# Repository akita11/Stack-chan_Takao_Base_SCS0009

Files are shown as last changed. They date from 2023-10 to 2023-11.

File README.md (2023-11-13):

# Stack-chan_Takao_Base_SCS0009

現時点で ｽﾀｯｸﾁｬﾝ を組み立てる最もシンプルな方法と思われる、[タカオさん](https://twitter.com/mongonta555)の[タカオ版](https://mongonta.booth.pm/)で[Feetech社のシリアルサーボSCS0009](https://www.switch-science.com/products/8042)を使うためのボードです。（※[SCS0009用のタカオ版筐体](https://github.com/mongonta0716/3DPrinter_Models)とあわせて使用できます。M5Stack本体と2個のシリアルサーボモータSCS0009用コネクタ、給電用のUSB TypeCコネクタがついたボードです。電源スイッチもついています。まるごと一式、タカオ版のサーボ固定部分(Bracket)に収納できます。市販のUSB Type-CコネクタつきのACアダプタ等をつないで給電して使用します。以下のように、本体の後ろ側からUSB Type-Cケーブルで給電して動作させることができます。

## 表面実装部品版

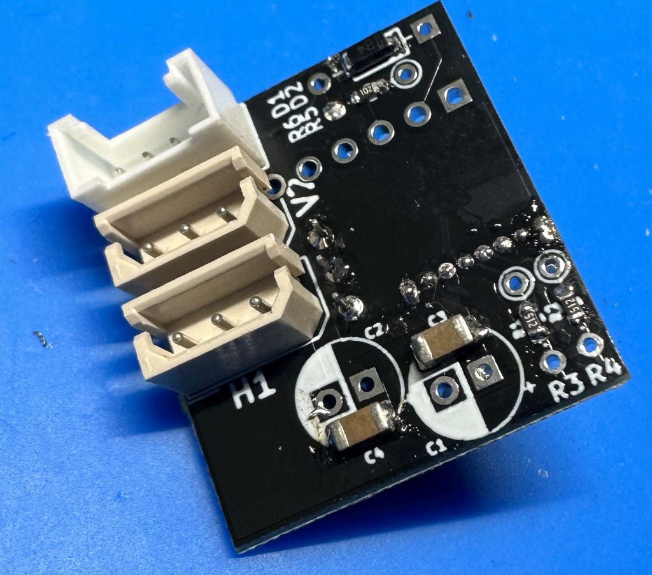
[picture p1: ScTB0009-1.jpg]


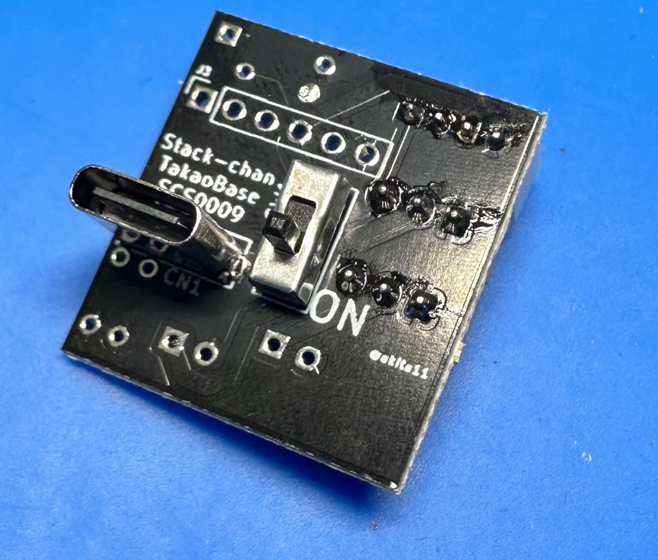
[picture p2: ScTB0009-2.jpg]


※完成品として[スイッチサイエンスで委託販売中](https://www.switch-science.com/products/9288)です

## 挿入実装部品版

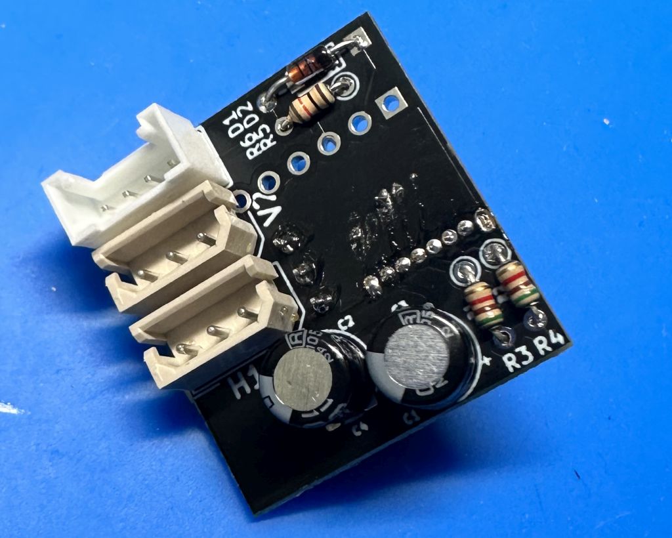
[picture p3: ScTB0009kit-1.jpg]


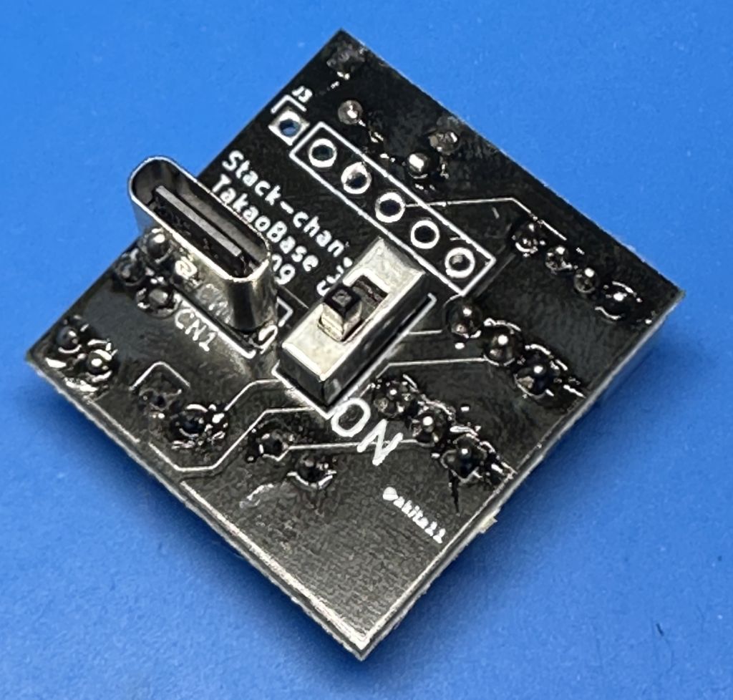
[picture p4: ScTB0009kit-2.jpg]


※部品キットとして[スイッチサイエンスで委託販売中](https://www.switch-science.com/products/9289)です

※部品キット版では、[組み立て手順](https://github.com/akita11/Stack-chan_Takao_Base_SCS0009/blob/main/Build/README.md)に沿って部品をはんだ付けしてください。

## 他に用意するもの

- M5Stack本体 (Core BasicまたはCore2がおすすめ）
- シリアルサーボモータ2個 [Feetech SCS0009](https://www.switch-science.com/products/8042)
- Groveケーブル ([M5Stack用5cm](https://www.switch-science.com/products/8664)など。すでにM5StackのUNITなどで余っているものがあればそれでもOK）
- 筐体[SCS0009用のタカオ版筐体](https://github.com/mongonta0716/3DPrinter_Models)を3Dプリント出力したものと必要なネジ類（[Boothで頒布中](https://booth.pm/ja/items/5186064)）

## 使い方

- 筐体の組み立てなどは、[タカオさんの手順](https://booth.pm/ja/items/5186064)を参考に行います。
- M5Stack本体と本ボードはGroveケーブルで接続します
- 2個のサーボを本ボードに接続します。ボード上の「H1」側には水平方向（足側）のサーボを、「V2」側には上下方向（筐体側）のサーボを接続します。いずれも、サーボのGND側（茶色や黒のケーブル側）を、本ボードの端側（白マークのある側）に挿し込みます。
- 本ボードを、Bracket（サーボを固定している部品）に収めます。必要に応じて両面テープやネジなどで固定してください。

## シリアルサーボSCS0009の設定

Feetech社のシリアルサーボSCS0009は、専用設定ツール[FD](https://gitee.com/ftservo/fddebug)を使ってIDや各種パラメータを設定することができます。特に今回のように2個のSCS0009を別々に使用する場合はそれぞれにIDを設定する必要があります。IDの初期値は1ですので、1つのSCC0009のIDを2に設定する必要があります。SCS0009の設定には[純正のボードFE-URT-1](https://akizukidenshi.com/catalog/g/gM-16295/)を使うこともできますが、このStack-chan_TakaoBaSE_SCS0009は簡易的に設定をするための回路が組み込まれています。ただし簡易的な回路のため、設定の読み出し・書き込みに失敗することもありますので、うまく読み出し・書き込みができない場合は、何度かリトライしてください。
※この回路は、[@washishi](https://twitter.com/washishi)さんの[Xでの投稿](https://twitter.com/washishi/status/1589990730822725632)を参考にしました。

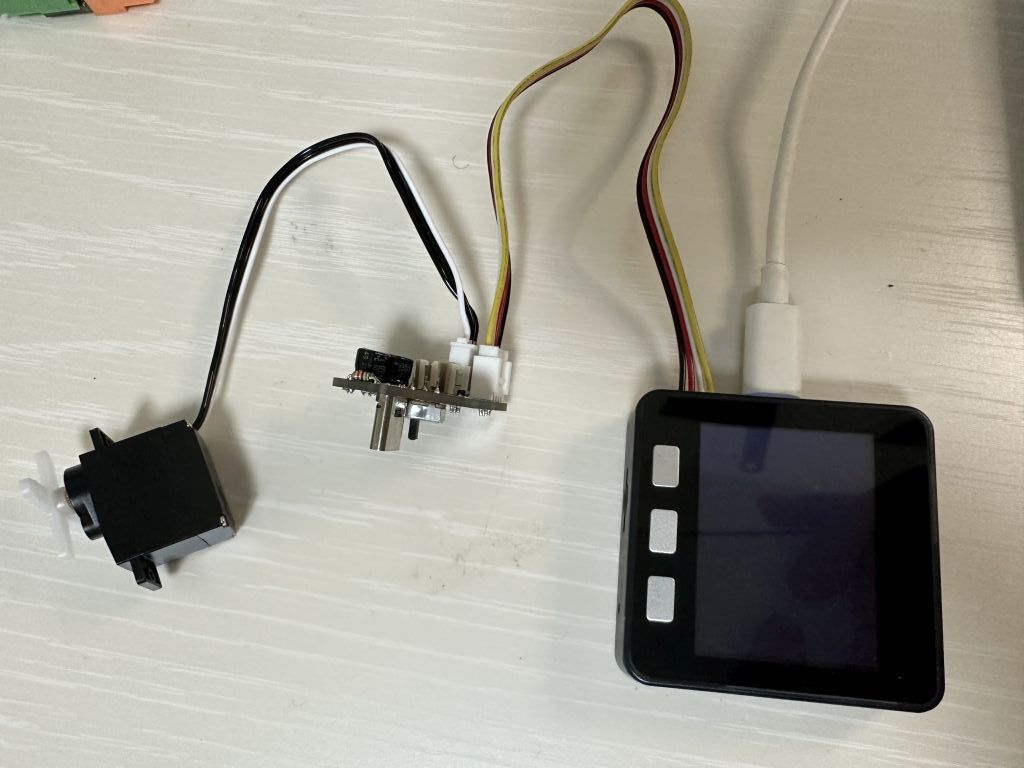
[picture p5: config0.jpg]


M5Stack(Basic/Core2)、本ボード、IDを変更するSCS0009（どちらのコネクタでもOK）を接続する。M5Stackには、設定用プログラムを書き込んでおく。（フォルダSCS0009testをVisualStudioCodeで開き、PlatformIOでビルド・書き込みする。必要に応じてplatformio.iniのボード指定を変更する（標準ではCore2用で、[env]内のdefault_envsで切り替え可能））

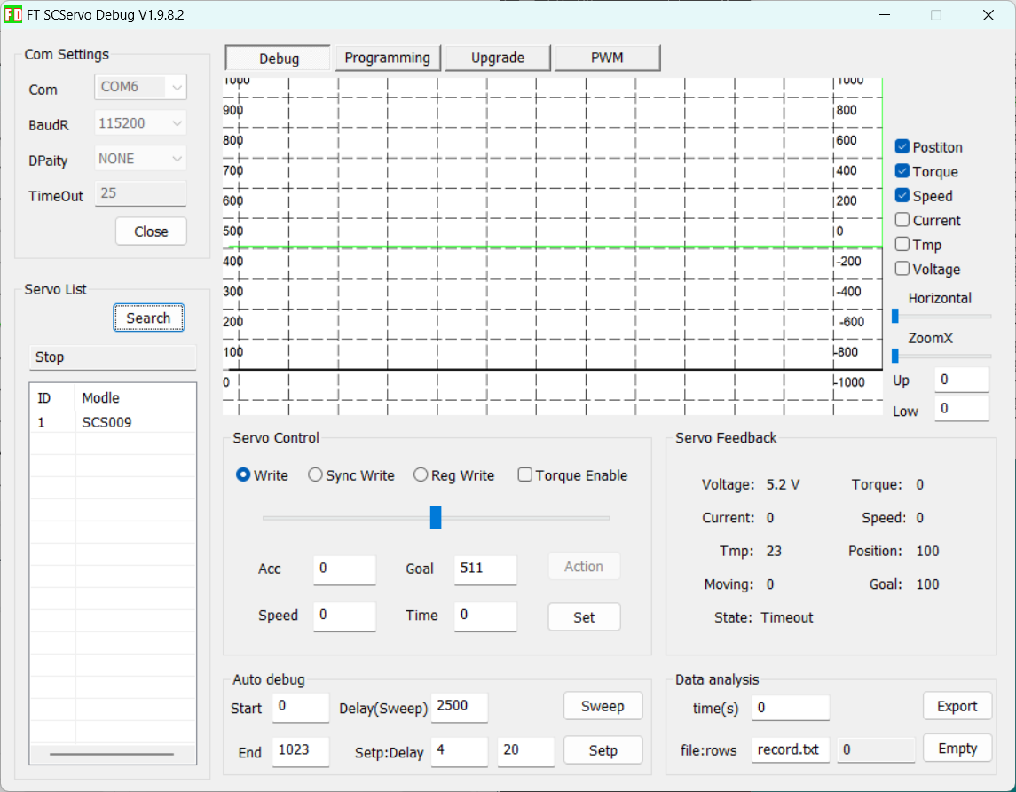
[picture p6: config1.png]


M5StackをPCに接続し、BaudRateを115,200を選んでそのCOMポートを開く。その後、”Search"を押すと、接続されているSCS0009が現れる（※出てこない場合はリトライしたり、USBケーブル抜き差しやM5Stackのリセット後にリトライする）

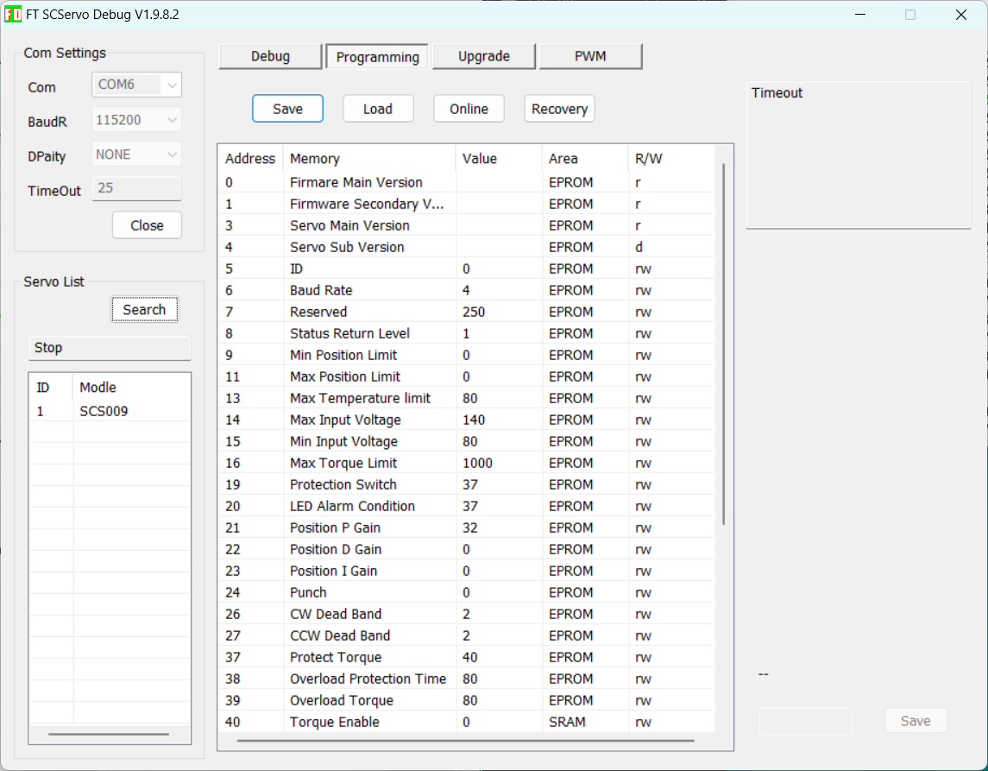
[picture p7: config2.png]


ID=1のSCS0009が見つかるはずなので、それを選択し、"Progamming"タブ内を開く。その中の"5.ID"を選ぶと、右下にIDを設定するボックスが現れるので、ここに"2"を入力して"Save"する。

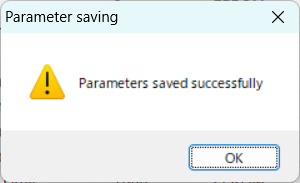
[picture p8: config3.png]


正しくIDが設定されればOK。念のため再度"Search"して、ID=2のSCS0009が見つかることを確認する。設定エラーが出る場合はリトライする。

## Author

Junichi Akita (akita@ifdl.jp, @akita11)

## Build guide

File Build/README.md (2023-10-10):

# Stack-chan_Takao_Base_SCS0009（部品キット版）の作り方





挿入実装部品版（部品キット版）の組み立て手順です。

## 用意するもの（部品一式）

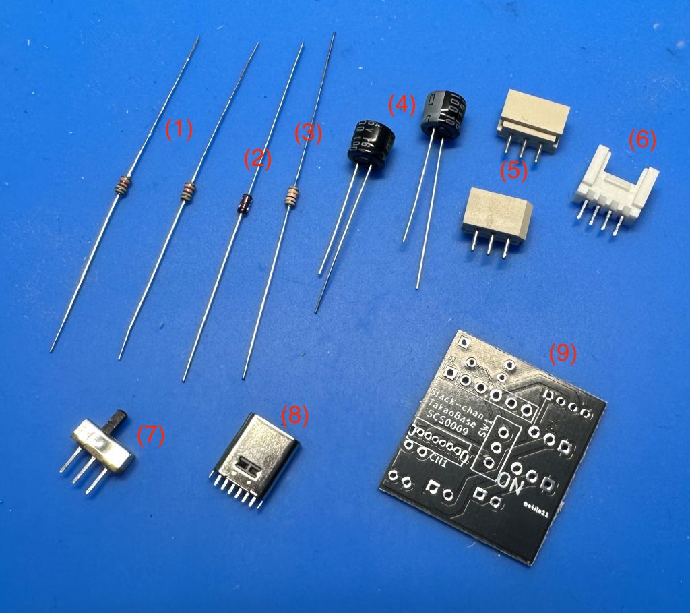
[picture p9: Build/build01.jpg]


- (1)抵抗(5.1kΩ:緑の帯がある方)：2本
- (2)ダイオード：1本
- (3)抵抗(1kΩ:緑の帯がない方)：1本
- (4)コンデンサ(100uF)：2個
- (5)サーボ用コネクタ：2個
- (6)Groveコネクタ：1個
- (7)電源スイッチ：1個
- (8)USB Type-Cコネクタ：1個
- (9)基板：1個

## 抵抗のとりつけ（その１）

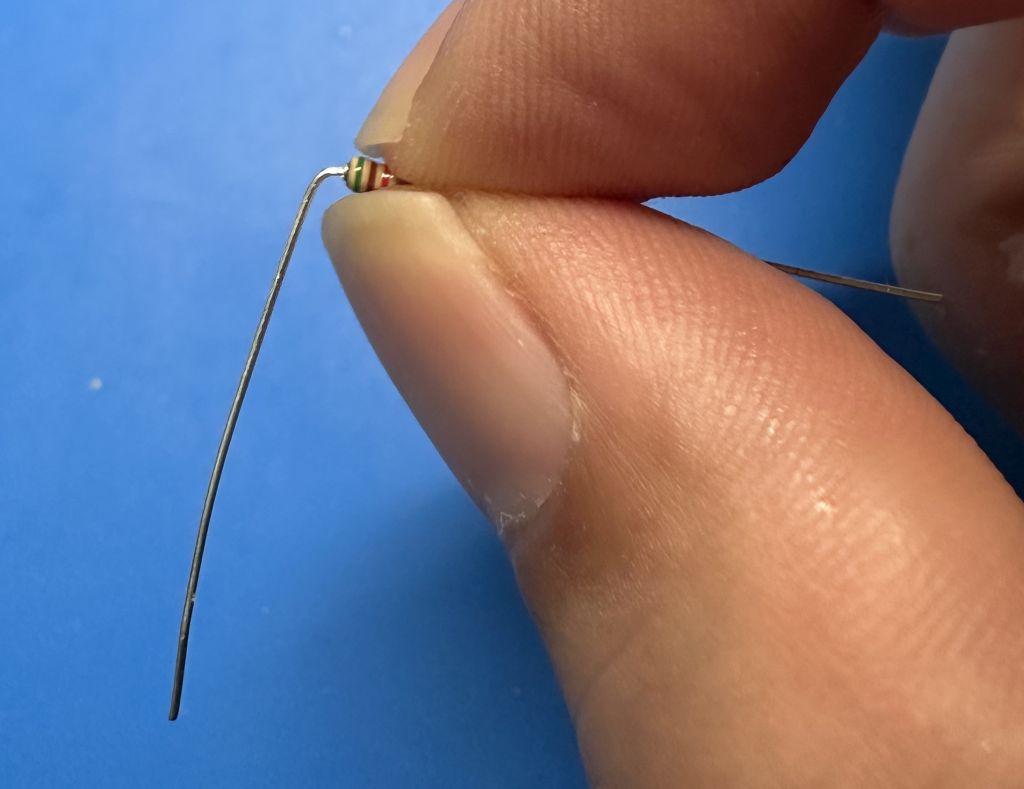
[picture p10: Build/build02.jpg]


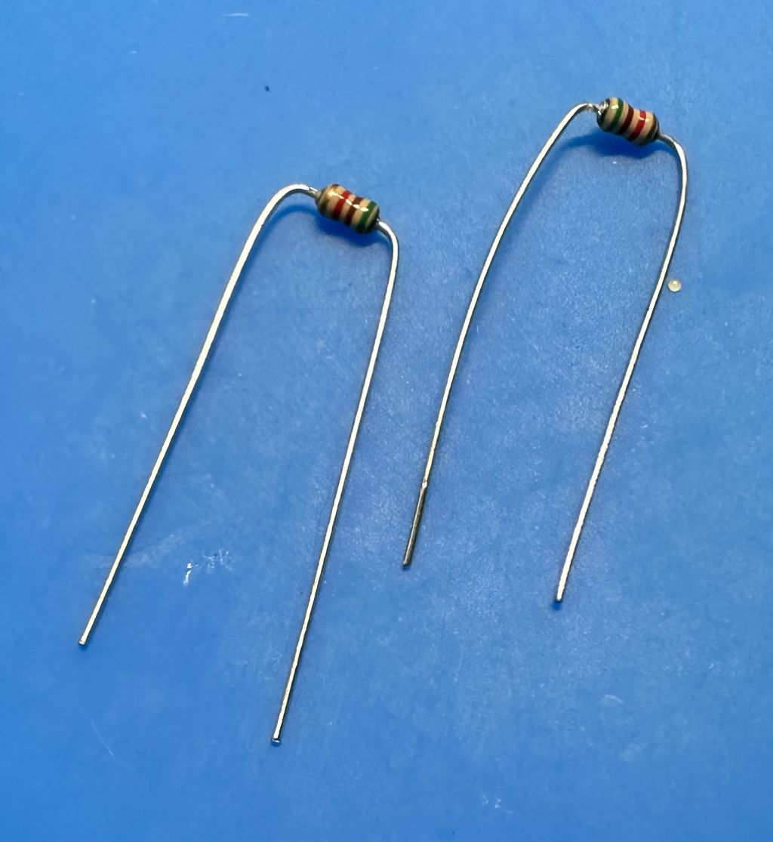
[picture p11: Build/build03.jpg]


(1)抵抗(5.1kΩ)の足を、これぐらいの間隔で90度に折り曲げます。根本に爪をあてると曲げやすいです。

それを(9)基板のこの位置（R3,R4の表示）に、奥まで差し込みます。

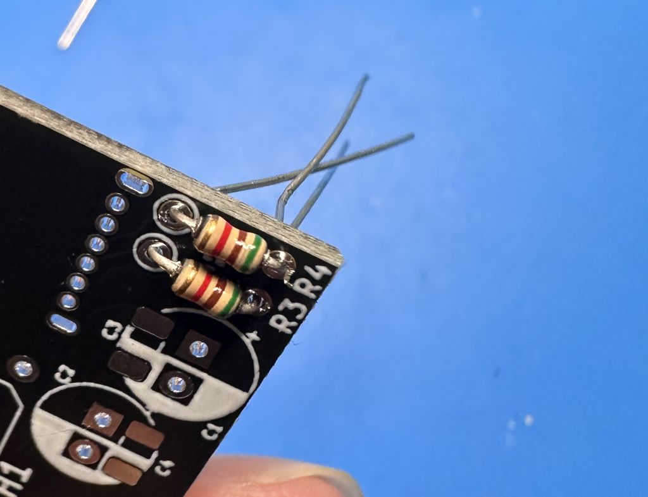
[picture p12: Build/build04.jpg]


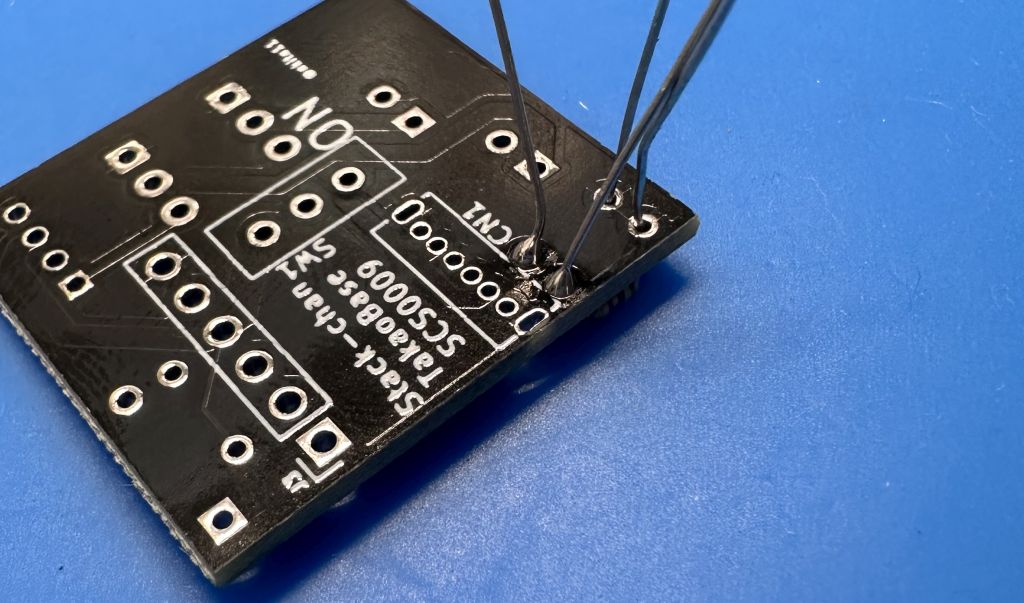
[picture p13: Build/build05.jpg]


それぞれの(1)抵抗の片側をはんだ付けします

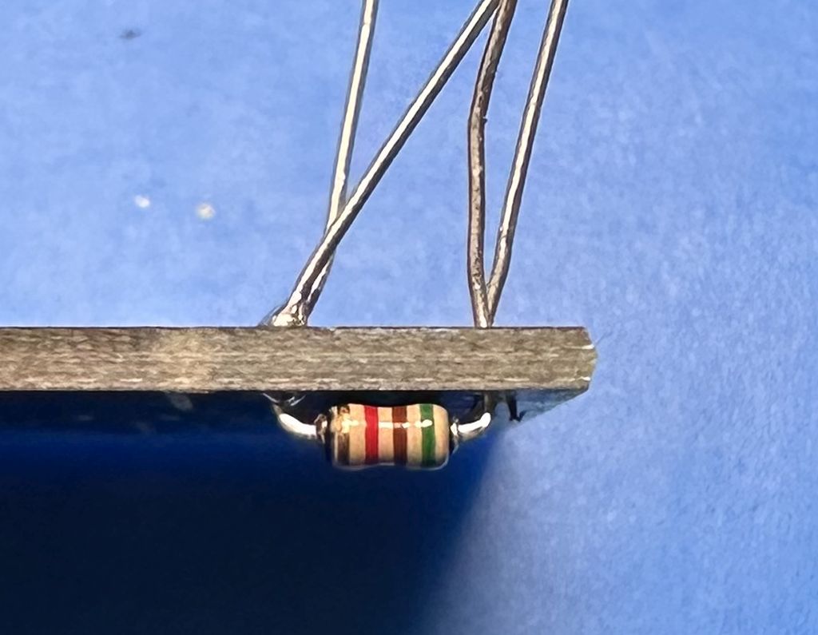
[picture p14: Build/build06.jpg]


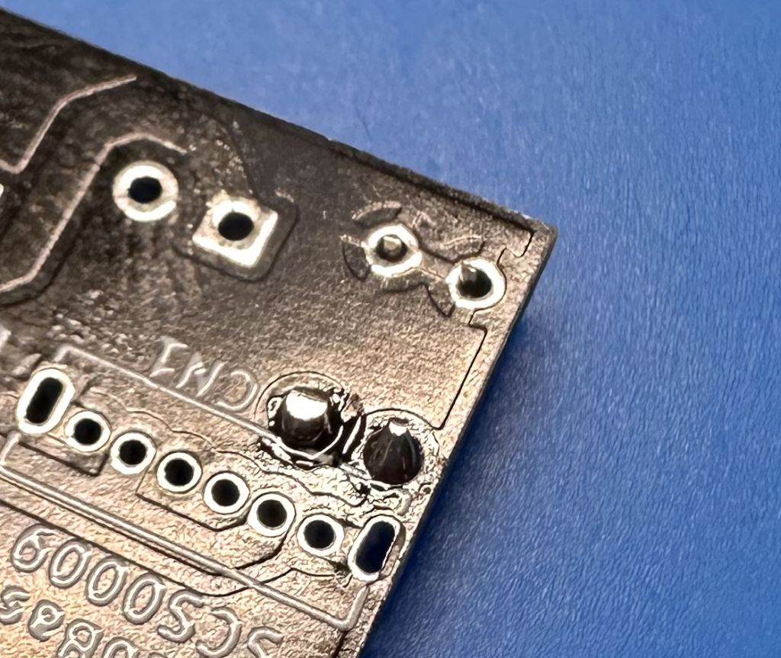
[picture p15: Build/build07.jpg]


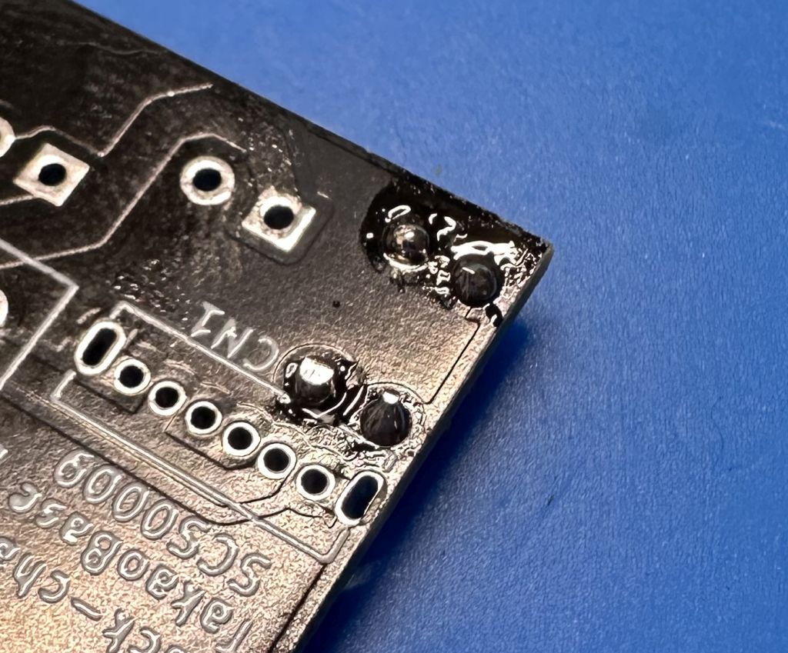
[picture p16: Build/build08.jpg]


表面で(1)抵抗が(9)基板から浮いていないことを確認し（浮いていたら、はんだを溶かしながら押し込む。多少は浮いていてもOK）、足を切って、残りの足をはんだ付け。

## ダイオードのとりつけ

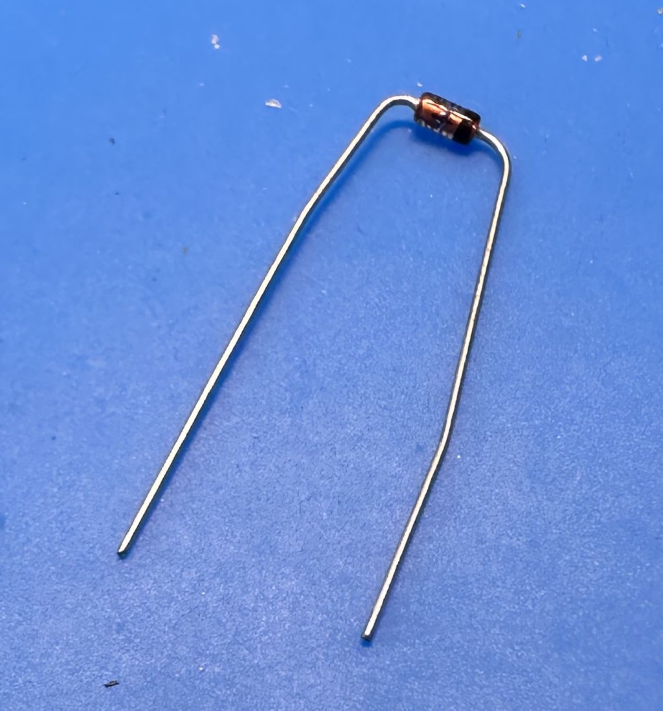
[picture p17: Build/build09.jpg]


(2)ダイオードの足を根本の近くから折り曲げる。

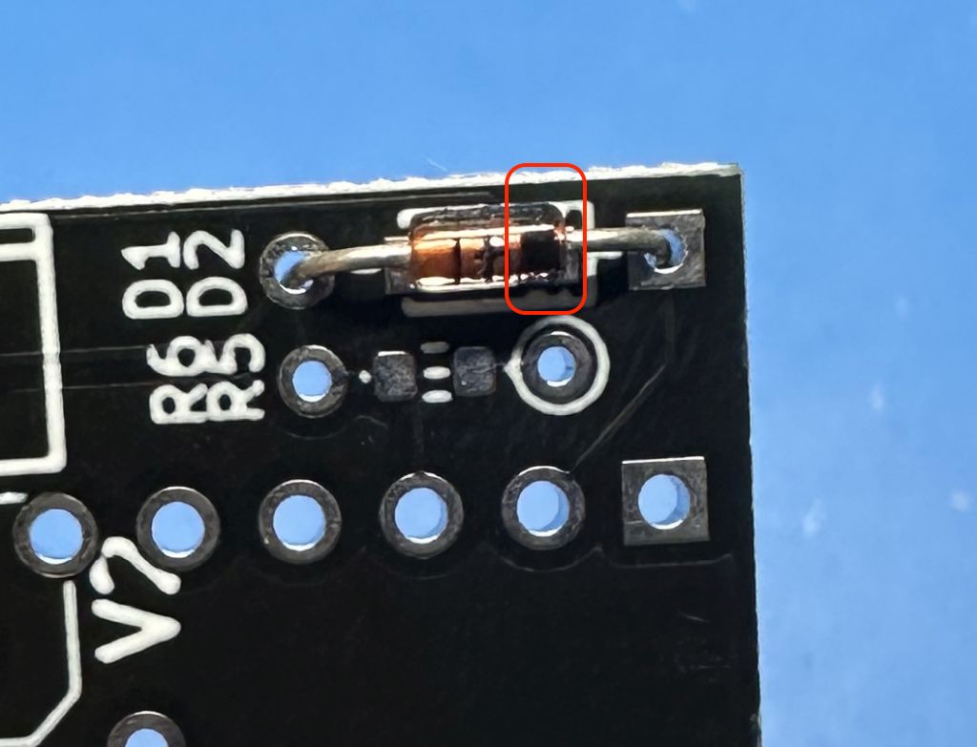
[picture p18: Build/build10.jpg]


(2)ダイオードを、(9)基板のこの位置（D1/D2の表示あり）に差し込む。<em>向きに注意（(2)ダイオードの黒い帯が、この写真の向きになるように）</em>

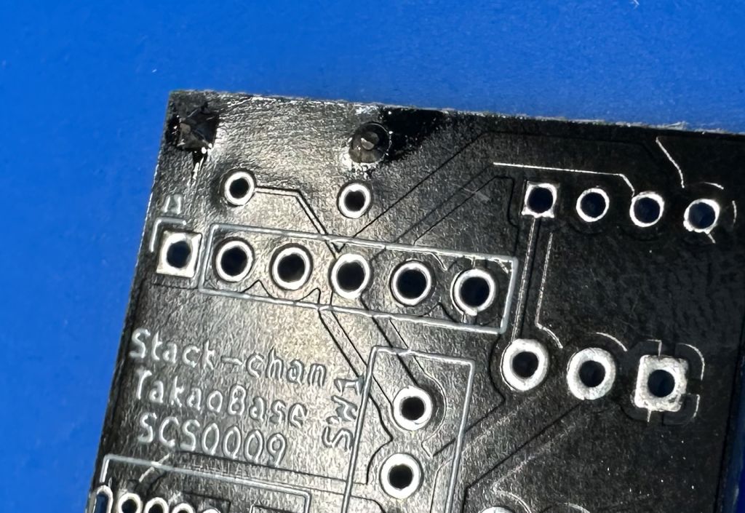
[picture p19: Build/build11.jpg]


その後、抵抗のときと同じように、片方の足をはんだ付け→浮いていないかを確認してから、もう片方のh足をはんだ付けする。

## 抵抗のとりつけ（その２）

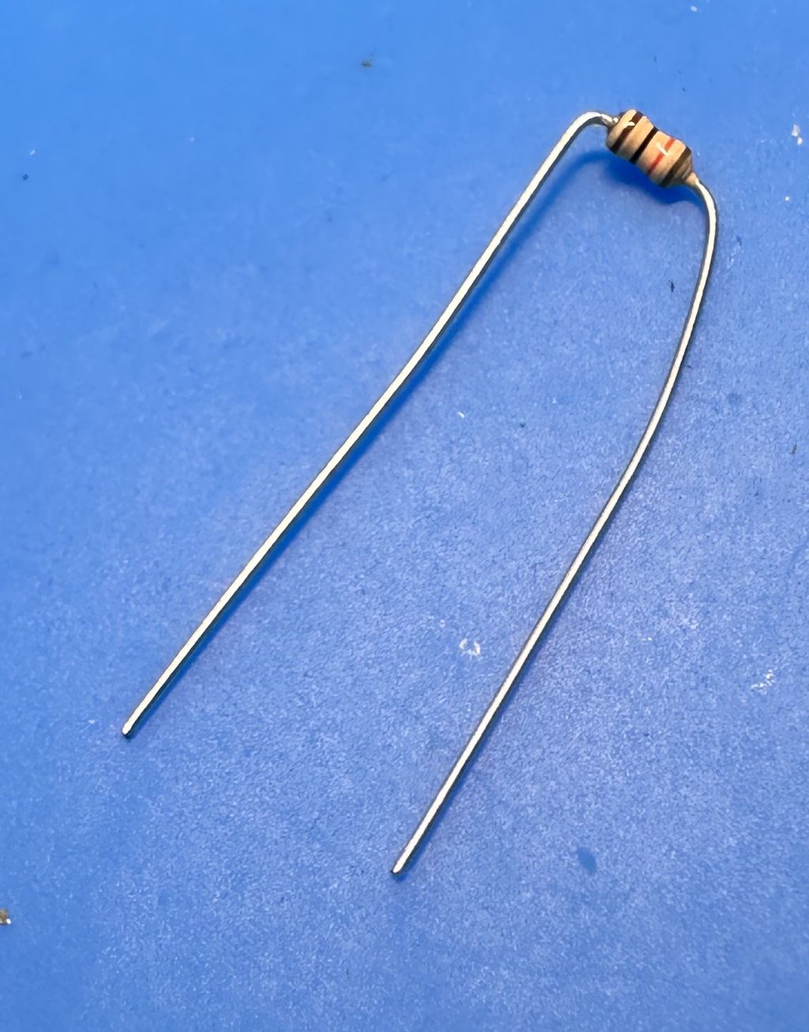
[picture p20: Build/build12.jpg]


(3)抵抗(1kΩ)の足を、同じように折り曲げる。

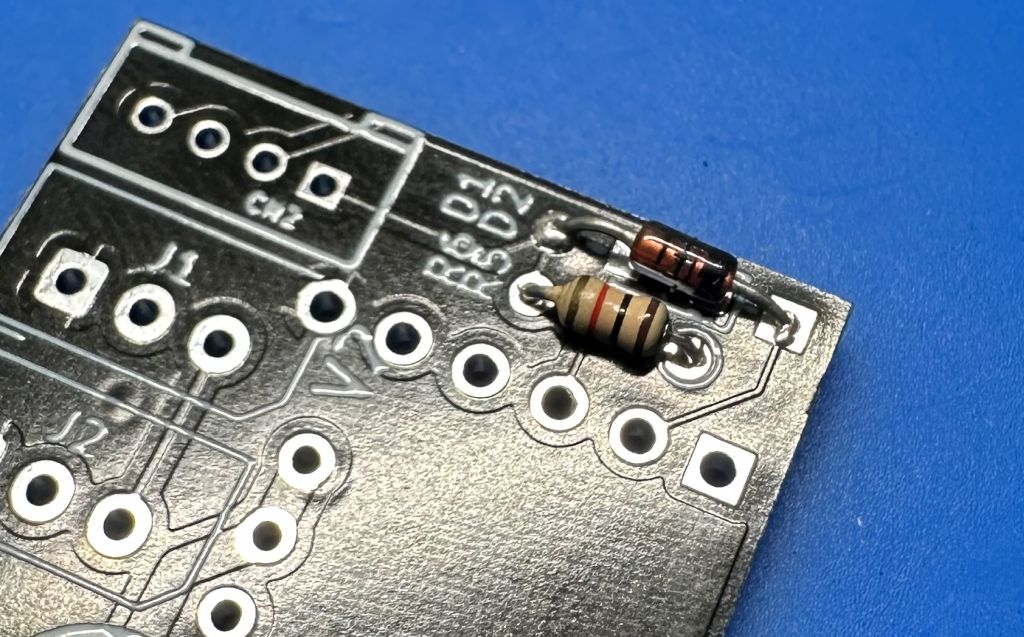
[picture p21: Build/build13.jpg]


基板のこの位置（R5/R6の表示あり）に差し込んで、同様に、はんだ付け。

## コンデンサのとりつけ

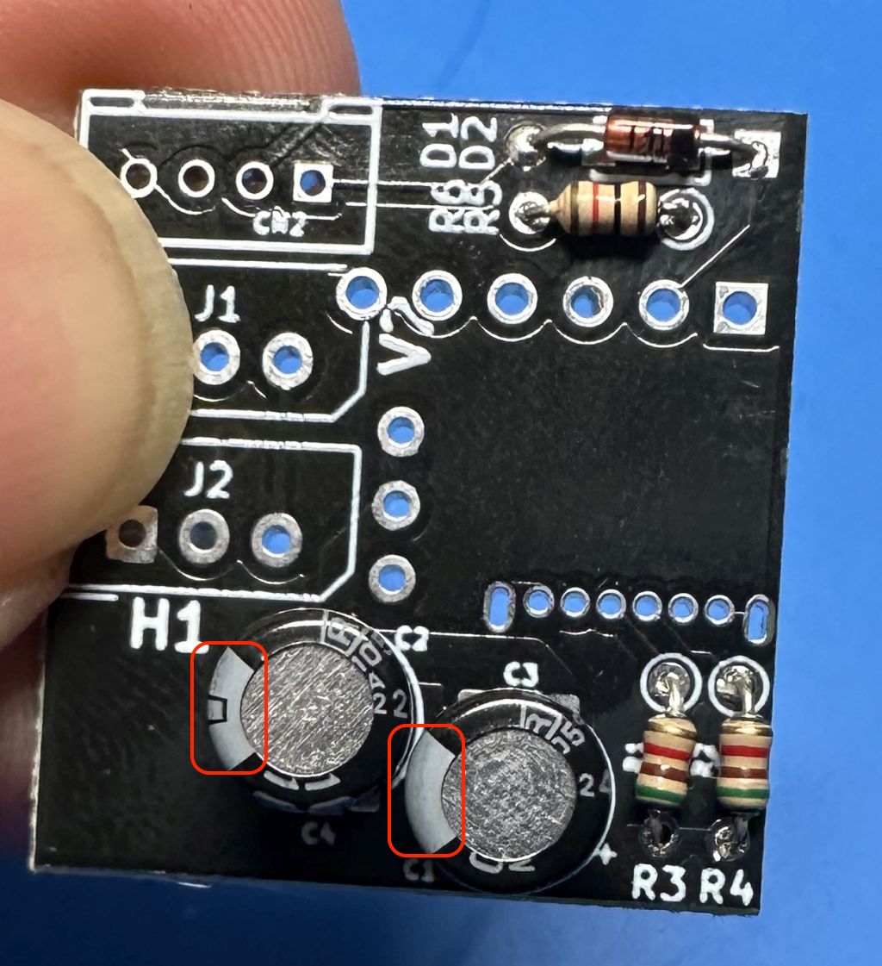
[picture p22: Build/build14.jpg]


(4)コンデンサを基板上のこのいちに差し込む。<em>コンデンサの白っぽいマークがこの向きになるように。</em>

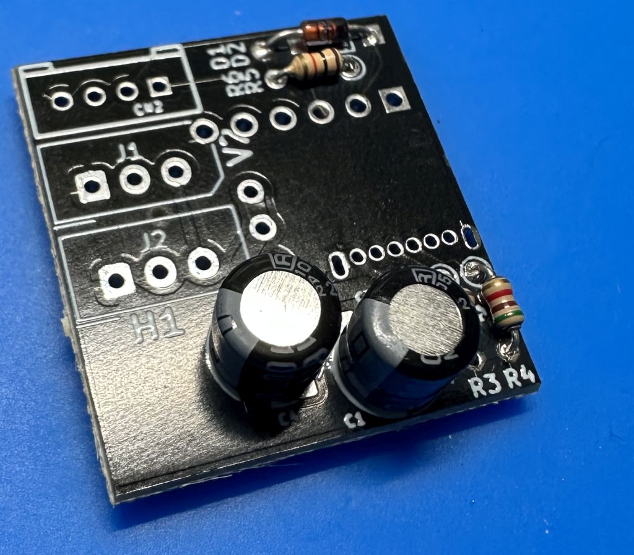
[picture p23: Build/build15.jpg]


奥までさしこみ、はんだ付け。

## サーボ用コネクタのとりつけ

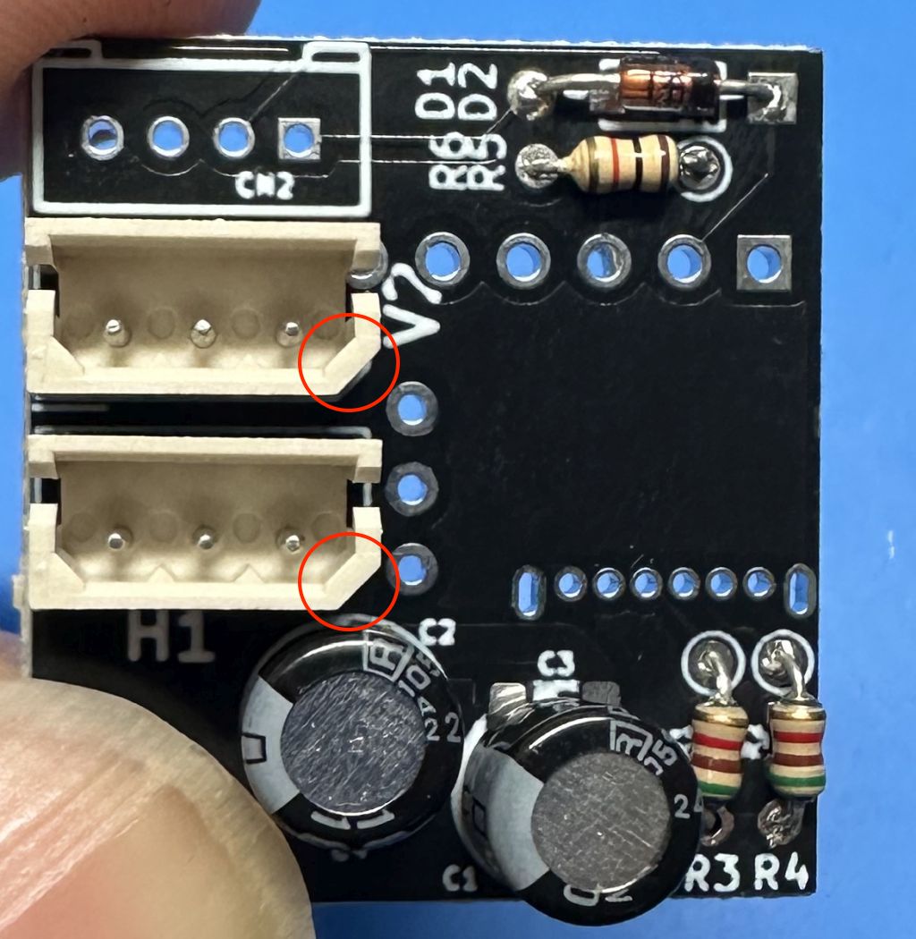
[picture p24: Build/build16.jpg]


(5)サーボ用コネクタを基板のこの位置に差し込む。<em>角が欠けている箇所がこの位置になるように注意。</em>

基板から浮かないように、何かで固定しながら、はんだ付け。抵抗などのときと同じように、まずは1箇所をはんだ付け後、浮いていたら、押さえながらはんだをとかして押し付けて、浮いていないのを確認後に、残りをはんだ付けするとよい。

## Groveコネクタのとりつけ

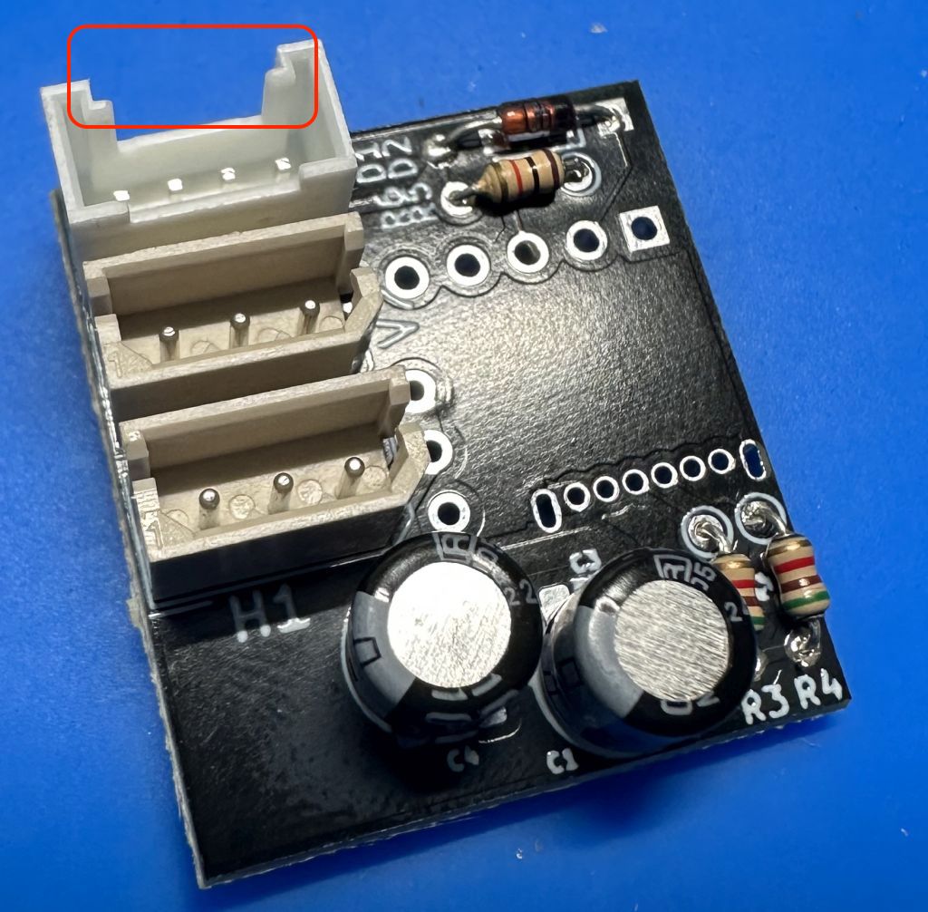
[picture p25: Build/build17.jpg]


(6)Groveコネクタを、赤丸の切り欠きの向きがこの通りになるようにさしこみ、浮かないように注意しながらはんだ付けします。

*※ここから先は、(9)基板の反対側の面に部品をとりつけます。(9)基板の部品を取り付ける位置に、白い四角い枠があるのを確認して部品をとりつけてください。くれぐれも逆側にとりつけないように注意！*

## 電源スイッチのとりつけ

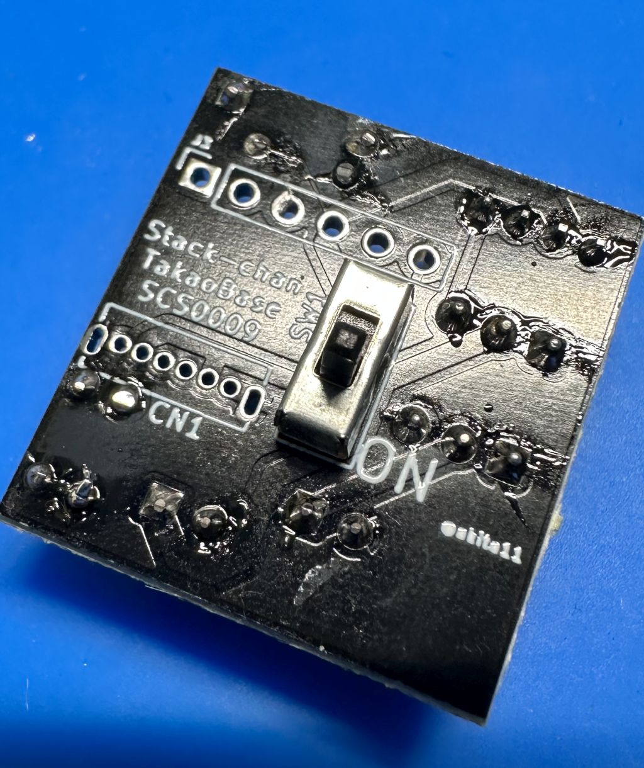
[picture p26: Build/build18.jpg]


(7)電源スイッチをさしこみます。



これまでと同じように、浮かないように注意しながら、まず1箇所、浮いていないのを確認してから、残りをはんだ付けします。



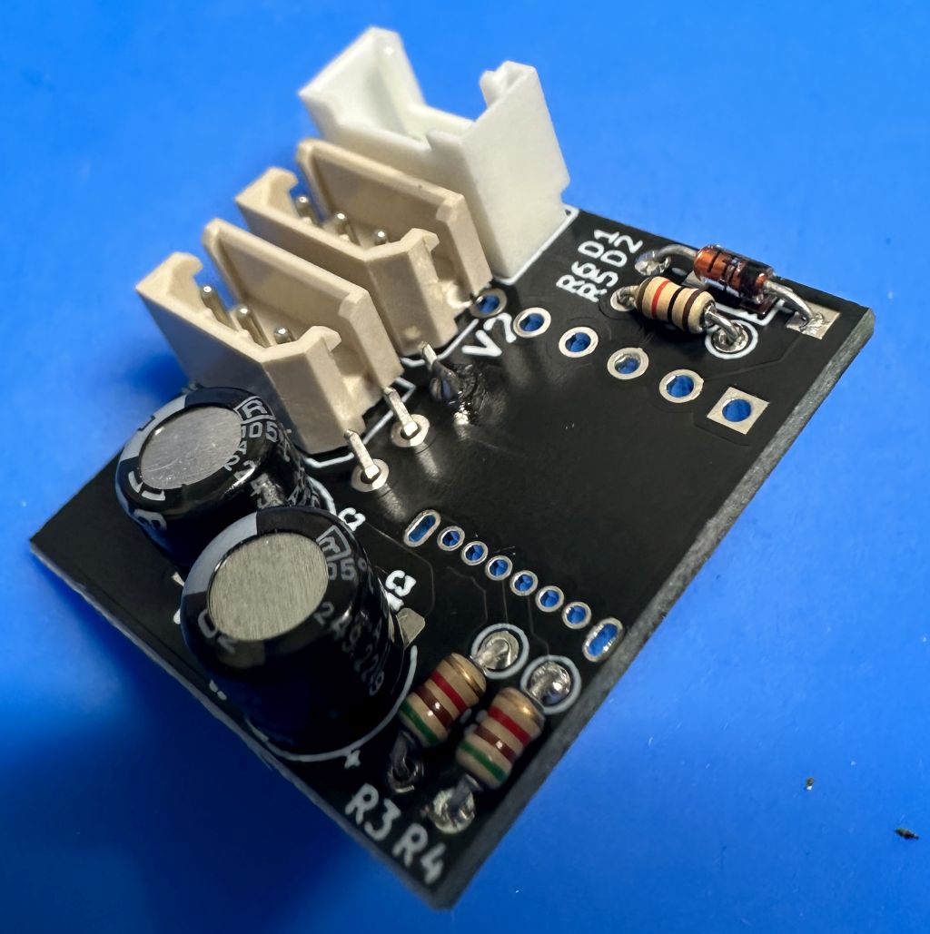
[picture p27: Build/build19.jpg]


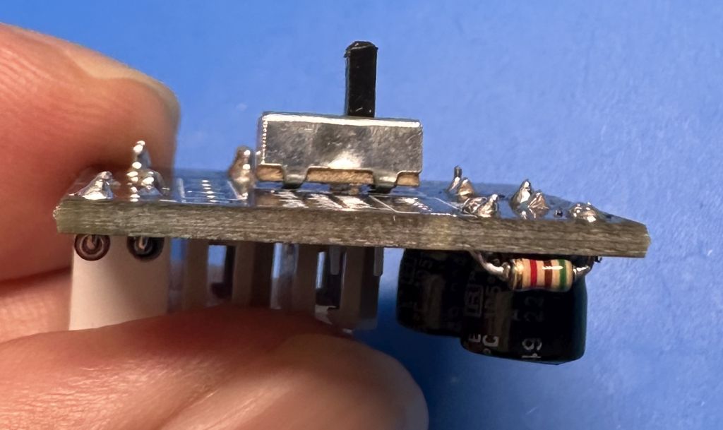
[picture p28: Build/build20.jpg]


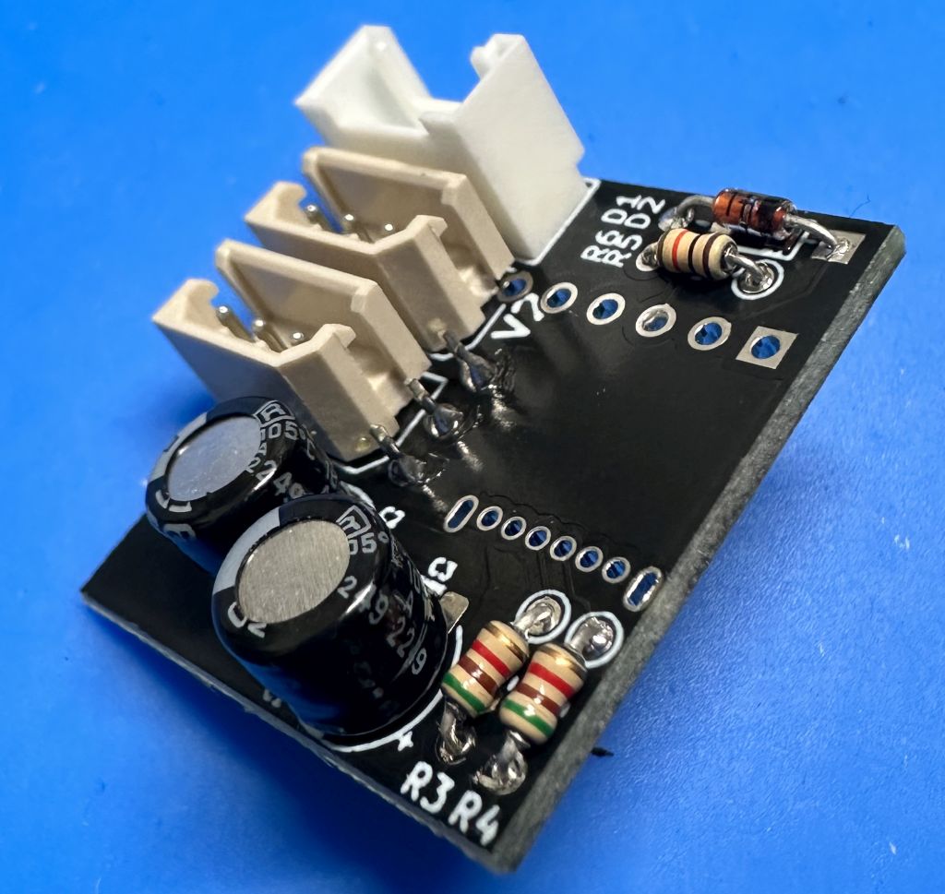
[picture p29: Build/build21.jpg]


## USBコネクタのとりつけ

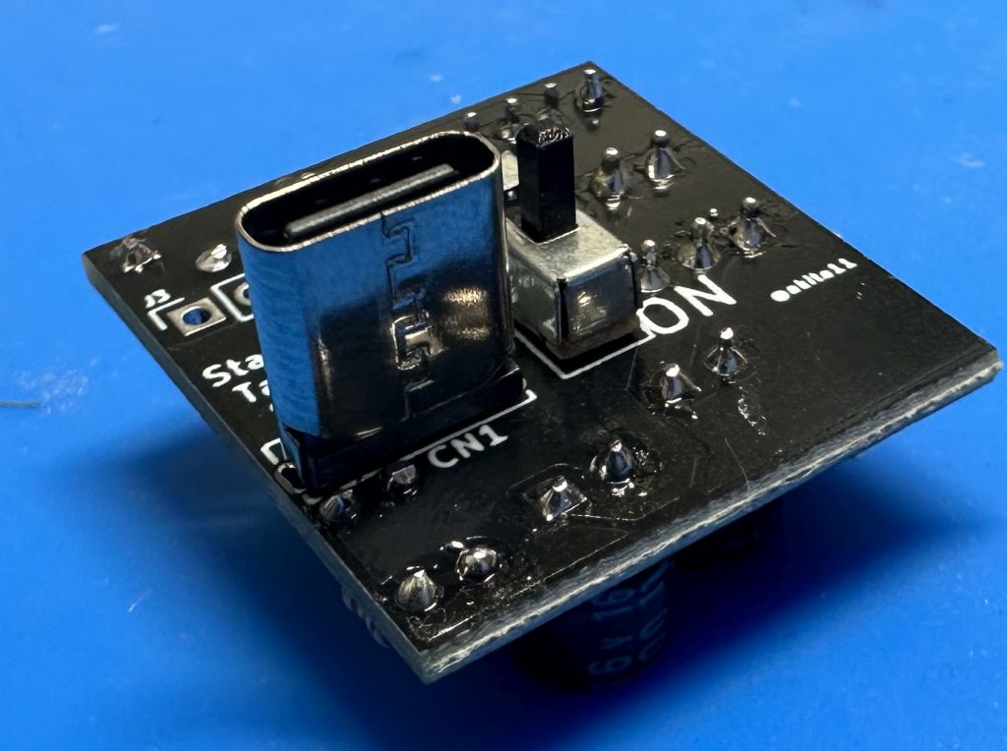
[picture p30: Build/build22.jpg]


(8)USBコネクタをさしこみます。

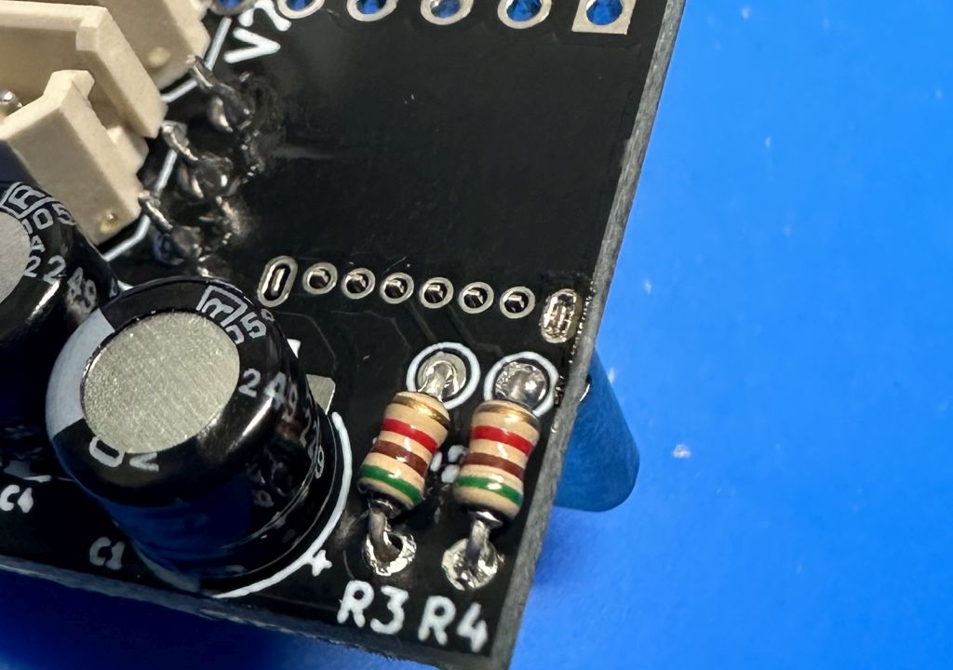
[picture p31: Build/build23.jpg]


浮かないように注意ながら、まず1箇所だけはんだ付けします。はんだ付けする箇所がとても小さいですが、はんだがとなりとショートしないようにはんだの量に注意します。もしはんだが多すぎてショートしてしまったら、あわてずにはんだごてでちょんちょんとすれば、はんだが取り除けます。
*端子の間隔が狭く、ショートしやすいので、十分に注意しましょう*

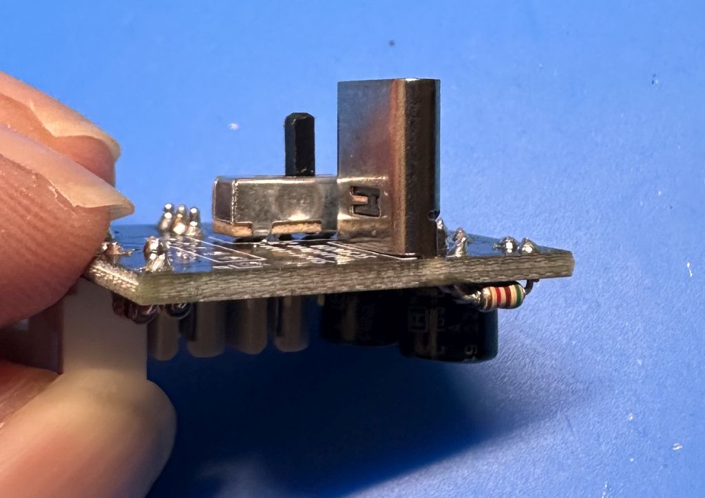
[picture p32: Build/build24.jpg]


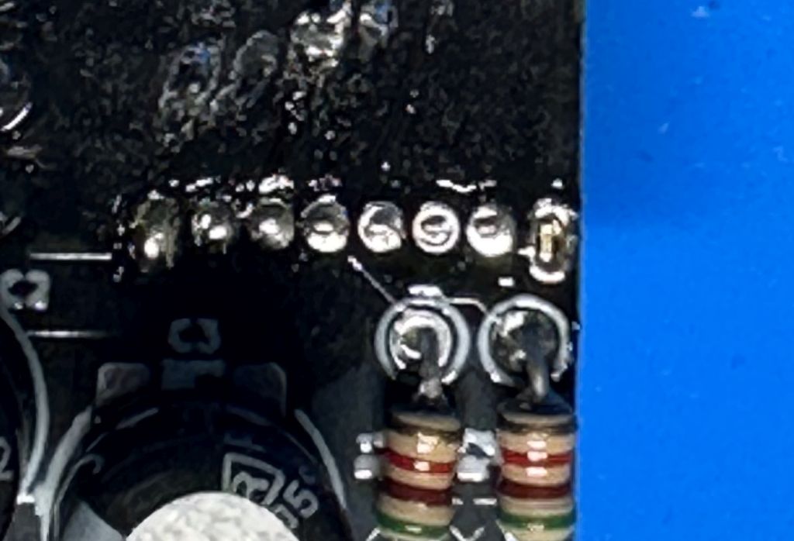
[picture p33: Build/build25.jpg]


浮いていないのを確認したら、残りをはんだ付けします。





完成！

## Author

Junichi Akita (akita@ifdl.jp, @akita11)

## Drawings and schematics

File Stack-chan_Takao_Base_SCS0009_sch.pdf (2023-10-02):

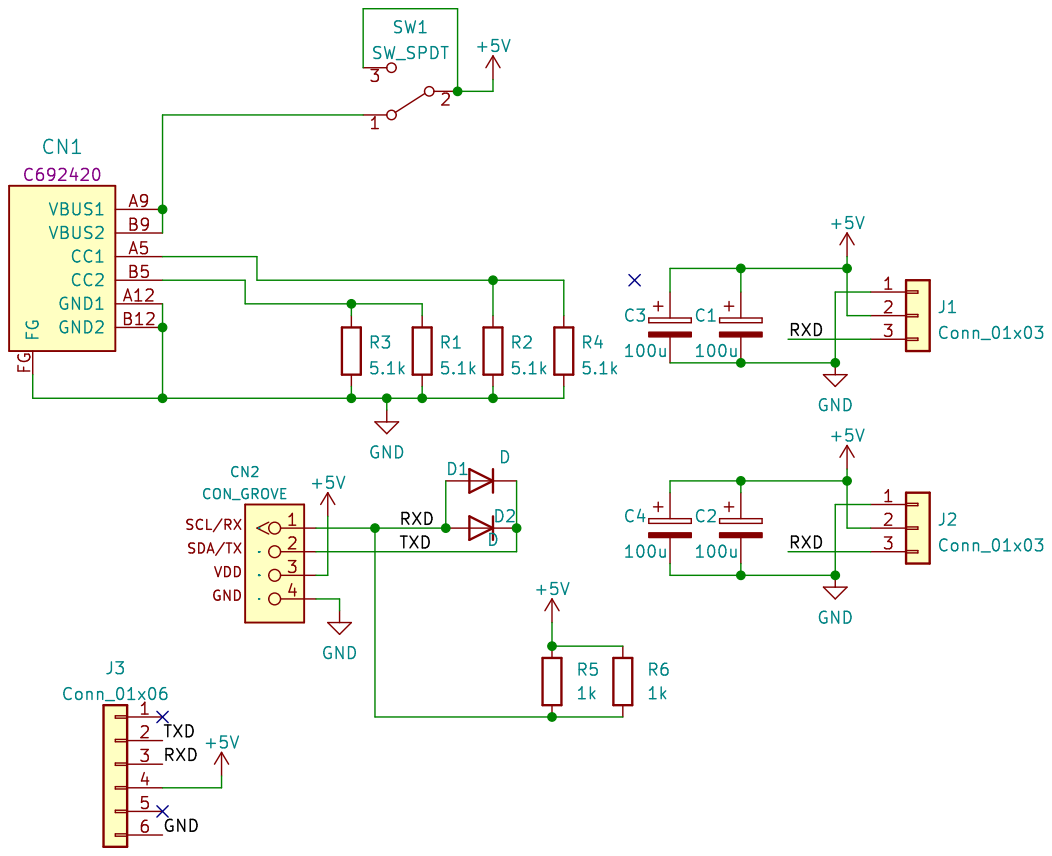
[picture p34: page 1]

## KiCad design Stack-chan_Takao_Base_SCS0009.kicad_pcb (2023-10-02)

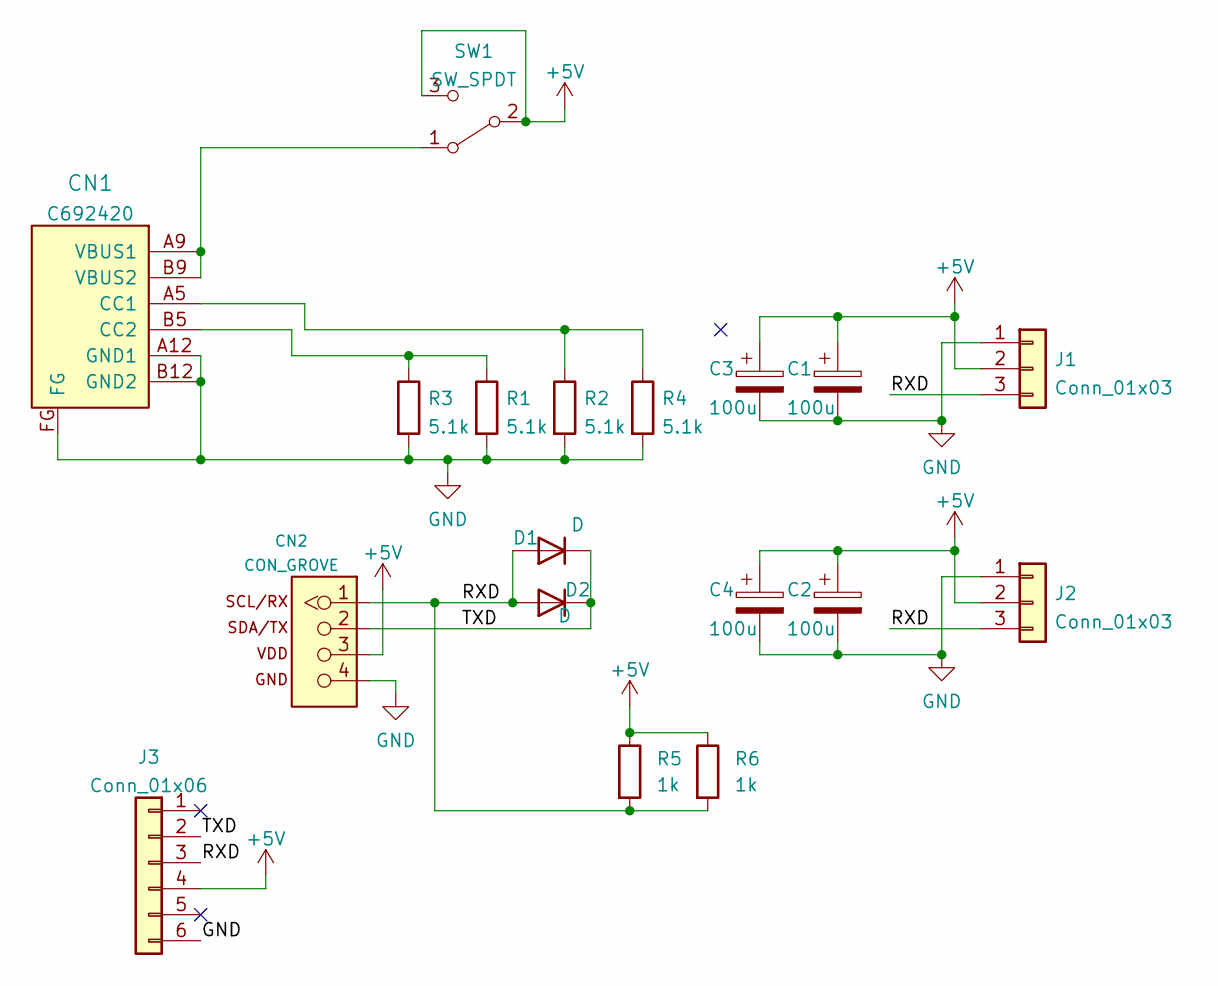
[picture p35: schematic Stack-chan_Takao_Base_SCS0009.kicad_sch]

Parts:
C1, C2: 100u; CP_Radial_D6.3mm_P2.50mm
C3, C4: 100u; C_1206_3216Metric
CN1: CON_USB-C-6; USB-C_6P_V_TH; LCSC C692420
CN2: CON_GROVE; CON_GROVE_V
D1: D; D_SOD-123F
D2: D; D_DO-34_SOD68_P7.62mm_Horizontal
J1, J2: Conn_01x03; Molex_SPOX_5267-03A_1x03_P2.50mm_Vertical
J3: Conn_01x06; PinSocket_1x06_P2.54mm_Vertical
R1, R2: 5.1k; R_0603_1608Metric
R3, R4: 5.1k; R_Axial_DIN0204_L3.6mm_D1.6mm_P5.08mm_Vertical
R5: 1k; R_Axial_DIN0204_L3.6mm_D1.6mm_P5.08mm_Vertical
R6: 1k; R_0603_1608Metric
SW1: SW_SPDT; SW_SPDT_9x4mm_W2.5mm

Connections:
+5V: C1.1, C2.1, C3.1, C4.1, CN2.3, J1.2, J2.2, J3.4, R5.1, R6.1, SW1.2 (B), SW1.3 (C)
/RXD: CN2.1, D1.2 (A), D2.2 (A), J1.3, J2.3, J3.3, R5.2, R6.2
/TXD: CN2.2, D1.1 (K), D2.1 (K), J3.2
GND: C1.2, C2.2, C3.2, C4.2, CN1.A12 (GND1), CN1.B12 (GND2), CN1.FG, CN2.4, J1.1, J2.1, J3.6, R1.2, R2.2, R3.2, R4.2
unnamed: CN1.A5 (CC1), R2.1, R4.1
unnamed: CN1.A9 (VBUS1), CN1.B9 (VBUS2), SW1.1 (A)
unnamed: CN1.B5 (CC2), R1.1, R3.1

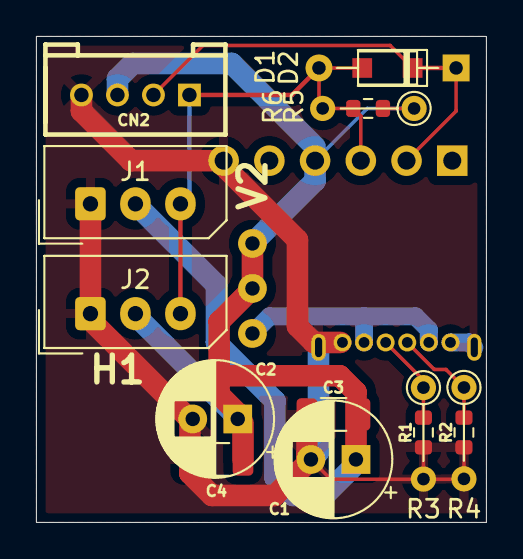
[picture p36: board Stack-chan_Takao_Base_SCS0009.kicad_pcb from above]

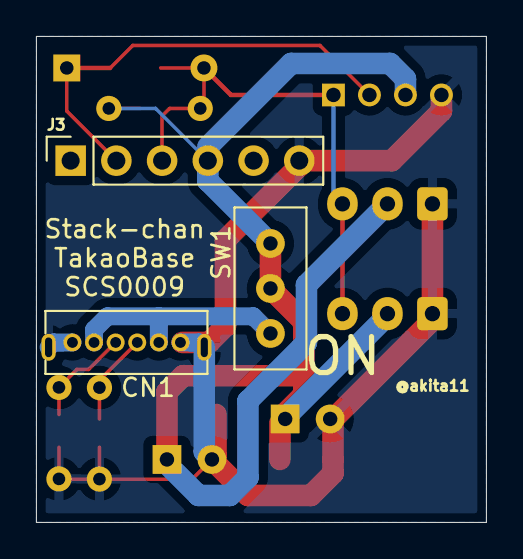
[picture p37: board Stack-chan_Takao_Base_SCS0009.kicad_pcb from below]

Board: 2 copper layers, 25.0 x 27.0 mm, 18 parts (3 on the bottom side), 7 nets.

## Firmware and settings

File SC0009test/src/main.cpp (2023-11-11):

// SerialPassthrogh for Stack-chan SCServo Model
#include <Arduino.h>
#include <M5Unified.h>

#define SerialSCS Serial1 // for Basic's PortA / RX/TX/V/G

void setup() {
  // Initialize M5Stack
  M5.begin(); 
  M5.In_I2C.release();  // Release internal I2C when using Port.A with UART.

  // Initialize SerialPort
  // for SCServo (Stack-chan bord include SignalConverter)
#if defined( ARDUINO_M5Stack_Core_ESP32 )
  SerialSCS.begin(1000000, SERIAL_8N1, 22, 21); // RX, TX
#elif defined(ARDUINO_M5STACK_Core2)
  SerialSCS.begin(1000000, SERIAL_8N1, 33, 32); // RX, TX
#elif defined(ARDUINO_M5Stack_ATOM)
  SerialSCS.begin(1000000, SERIAL_8N1, 32, 26); // RX, TX
#endif
}
void loop() {
  // PC to SCServo
  if (Serial.available()) {
    int inByte = Serial.read();
    SerialSCS.write(inByte);
    SerialSCS.flush(); // wait send
    SerialSCS.read(); // flash call back
  }
  // SCServo to PC
  if (SerialSCS.available()) {
    int inByte = SerialSCS.read();
    Serial.write(inByte);
    Serial.flush(); // wait send
  }
  M5.update();
}
